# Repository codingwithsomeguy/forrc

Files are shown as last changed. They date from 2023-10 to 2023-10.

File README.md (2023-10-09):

# FORRC - Free and Open RC Robot Car

Welcome to the FORRC repository! FORRC is a basic remote controlled car
that's designed to be a low cost 3d printable car to learn about building
small cars from scratch. The designs are available in FreeCAD and as
exported STL files, and the Bill Of Materials (BOM) is included based
on readily available off the shelf parts.

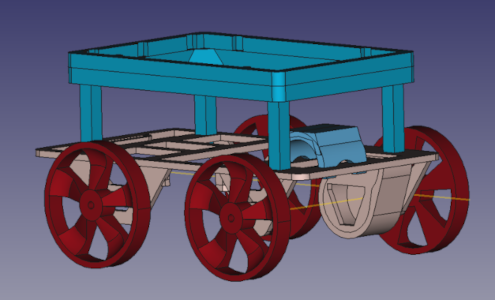
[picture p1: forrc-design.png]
FORRC Design


Note that the FreeCAD file uses the [freecad.gears](https://github.com/looooo/freecad.gears) / FCGear external workbench, available in the Addon Manager.

## Kits
Kits are also available from the Fairfield County Makers' Guild (FCMG)
close to cost, with a small markup for packing/collating and a small
donation. Any profits derived from purchasing a kit goes towards
supporting the FCMG, a 501(c)(3) nonprofit located in Norwalk, CT.
Unless you're purchasing a very large quantity of cars, the kit probably
costs less than buying all of the parts individually, but feel free
to source your own parts! At the time this was created, the kit cost a
bit less, but YMMV. Your support is always appreciated.

## Practical Info
The unmodified base car is geared down for relatively low speeed use.
Feel free to modify the design to add a higher speed motor! For
educational purposes and for the low end microcontroller included, the
lower speeds are easier on the hardware, but it's always fun to go zoom as
well.

The STL files can be loaded into a slicer such as cura but may need to be
flipped over to lie flat on the print bed. Total print time for all the
parts is around 10-20 hours depending on your printer's speed, or the
designs can be sent off to a contract print company for a nominal fee. The
full car (without a body, you'd need to design your own if you want)
takes about 30g of material (test prints were done with PLA).

## Class
If you'd like to build your car and learn about the drive mechanics in person, feel free to sign up for a class at [Fairfield County Makers' Space](https://fcmakers.com) or like minded nearby makerspaces. The course outline will be posted in due time.

## License
These designs, files, and hardware are licensed under the CERN-OHL-S v2 Open Hardware Licence - Strongly Reciprocal. See [License](LICENSE.txt) for the full license text or [CERN's Open Hardware Licence site](https://ohwr.org/cern_ohl_s_v2.txt).

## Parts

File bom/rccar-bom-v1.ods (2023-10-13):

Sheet: BOM
Quantity | Item | Description | Link | Gross Price | Gross Units | Unit Price | Quantity Needed Price
1 | small breadboard | DEYUE breadboard Set Prototype Board - 6 PCS 400 Pin Solderless Board Kit for Raspberry pi and Arduino Project | https://www.amazon.com/dp/B07LFD4LT6 | $7.99 | 6 | $1.33 | $1.33
4 | #61 rubber band | Alliance Rubber 54615 Advantage Rubber Bands Size #61, 1 lb Box Contains Approx. 535 Bands (2inch x 1/4inch, Blue) | https://www.amazon.com/dp/B008X09UNC | $7.58 | 535 | $0.01 | $0.06
1 | MT3608 boost DCDC | 8Pcs DC-DC Adjustable Boost Module 2A DC Voltage Regulator Boost Plate Step Up Converter Module with USB 2V-24V to 5V 9V 12V 28V | https://www.amazon.com/dp/B09ZKKFHXW | $7.99 | 8 | $1.00 | $1.00
1 | battery holder w/leads | QTEATAK 4 x 1.5V AA Batteries Battery Holder Wire Leads | https://www.amazon.com/dp/B085VS14TY | $6.99 | 4 | $1.75 | $1.75
20 | jumpers | AUSTOR 560 Pieces Jumper Wire Kit 14 Lengths Assorted Preformed Breadboard Jumper Wire with Free Box | https://www.amazon.com/dp/B07CJYSL2T | $11.99 | 560 | $0.02 | $0.43
10 | F/M jumper cables long | EDGELEC 120pcs 20cm Dupont Wire Male to Female Breadboard Jumper Wires 7.9 inch 1pin-1pin 2.54mm Connector for DIY Arduino Raspberry PI 10 15 20 30 40 50 100cm Optional Multicolored Ribbon Cables | https://www.amazon.com/dp/B07GD1TFBR | $7.98 | 120 | $0.07 | $0.67
10 | F/M jumper cables short | EDGELEC 120pcs 10cm Dupont Wire Male to Female Breadboard Jumper Wires 3.9 inch 1pin-1pin 2.54mm Connector for DIY Arduino Raspberry PI 10 15 20 30 40 50 100cm Optional Multicolored Ribbon Cables | https://www.amazon.com/dp/B07GD1R5MS | $6.98 | 120 | $0.06 | $0.58
1 | M2 / 10mm | HELIFOUNER 560 Pieces M2 x 4mm /6mm /8mm /10mm /12mm /16mm /20mm, Countersunk Head Socket Cap Screws Bolts Washers Nuts Kit, 304 Stainless Steel | https://www.amazon.com/dp/B0B6HZX2ZJ | $11.99 | 140 | $0.09 | $0.09
2 | M2 / 8mm | (same set) |  |  |  | $0.09 | $0.17
2 | M2 Nuts | (same set)
1 | flyback diode 4004 | BOJACK 1N4004 Rectifier Diode 1 A 400 V DO-41 Axial 4004 1 amp 400 Volt Electronic Silicon Diodes(Pack of 125 Pieces) | https://www.amazon.com/dp/B07Q4F4RPZ | $5.99 | 125 | $0.05 | $0.05
4 | resistors for LEDs | EDGELEC 100pcs 220 ohm Resistor 1/2w (0.5Watt) ±1% Tolerance Metal Film Fixed Resistor, Multiple Values of Resistance Optional | https://www.amazon.com/dp/B07QK9ZBVZ | $5.99 | 100 | $0.06 | $0.24
1 | M2 hex wrench | Tsnamay 2mm Hex Key Wrench L Shaped Hexagon Head Repairing Tool 50pcs | https://www.amazon.com/dp/B09R98WLZ2 | $6.99 | 50 | $0.14 | $0.14
4 | LEDs | BOJACK 5 Colors 500 pcs 5mm LED Diode Lights Assored Kit Pack Bright Lighting Bulb Lamps Electronics Components 5 mm Light Emitting Diodes Parts | https://www.amazon.com/dp/B09XDMJ6KY | $11.99 | 500 | $0.02 | $0.10
1 | BJT | MCIGICM (200 Pcs) 2N2222 Transistor, 2N2222A to-92 Transistor NPN 40V 600mA 300MHz 625mW Through Hole | https://www.amazon.com/dp/B06XPWS52G | $6.99 | 200 | $0.03 | $0.03
1 | L293D motor controller | Bridgold 10pcs L293 L293D 16-pin IC Stepper Motor Drivers Controllers | https://www.amazon.com/dp/B07NXTWJV9 | $8.99 | 10 | $0.90 | $0.90
1 | shift register | (Pack of 25 Pieces) MCIGICM 74HC595 74595 SN74HC595N 8-Bit Shift Register DIP-16 IC 74hc595 Shift registers | https://www.amazon.com/dp/B07HFWB9L9 | $6.99 | 25 | $0.28 | $0.28
1 | esp32cam with CH340C usb card | DORHEA 4 Set ESP32 Cam WiFi Bluetooth Development Board with OV2640 Camera Module + Micro USB to Serial Port CH340C 4.75V-5.25V Nodemcu for Raspberry Pi | https://www.amazon.com/dp/B09265G5Z4 | $28.99 | 4 | $7.25 | $7.25
1 | geared dc N20 motor | Acxico 3Pcs Mini Micro N20 Gear Motor DC 3V-6V Slow Speed Full Metal Gearbox DIY Robot Car | https://www.amazon.com/dp/B09DG3GCGK | $9.99 | 3 | $3.33 | $3.33
1 | steering servo | Sg90 9g Micro Servo Motor, Miuzei Mini Servos Motor Kit Metal Gear 180 Degree Servo for Rc Car Airplane Plane Arduino 10 Pack | https://www.amazon.com/dp/B072V529YD | $18.88 | 10 | $1.89 | $1.89
1 | pack of servo horns | (same set)
1 | cut to 2pc 88mm rods for axles | TOP-VIGOR 20pcs 2mm x 300mm Stainless Steel Rods for DIY Crafts, Metal Solid Round Shaft Rods Lathe Bar Stock for DIY Car Helicopter Airplane Model | https://www.amazon.com//dp/B09WDCDCR6 | $9.59 | 20 | $0.48 | $0.48
48 | PLA | OVERTURE PLA Filament 1.75mm PLA 3D Printer Filament, 2kg Cardboard Spool (4.4lbs), Dimensional Accuracy +/- 0.03mm, Fit Most FDM Printer (White 2-Pack) | https://www.amazon.com/dp/B085DX3X8Y | $36.99 | 2000 | $0.02 | $0.89
 | subtotal with USB programmer |  |  | $227.86 |  |  | $21.64
-1 | esp32cam with CH340C usb card | DORHEA 4 Set ESP32 Cam WiFi Bluetooth Development Board with OV2640 Camera Module + Micro USB to Serial Port CH340C 4.75V-5.25V Nodemcu for Raspberry Pi | https://www.amazon.com/dp/B09265G5Z4 | $28.99 | 4 | $7.25 | -$7.25
1 | esp32cam without USB | 4PCS ESP32-CAM Camera Module ESP32 CAM WiFi Bluetooth Development Board ESP32 Wireless OV2640 Camera Module with Jumper Wire | https://www.amazon.com/dp/B08R8F2BWL | $24.99 | 4 | $6.25 | $6.25 | without the programmer (use an esp8266 or similar)
 | subtotal without USB programmer |  |  |  |  |  | $20.64
Not included:
0.05 | C-A glue | Loctite Super Glue Gel Control, Clear Superglue For Plastic, Wood, Metal, Crafts, & Repair, Cyanoacrylate Adhesive Instant Glue, Quick Dry - 0.14 fl oz Bottle, Pack Of 6 | https://www.amazon.com/dp/B0778LB4RX | $17.16 | 6 | $2.86 | $0.14
1 | small 2mm file | KALIM Mini Needle File Set (Carbon Steel 6 Piece-Set) Hardened Alloy Strength Steel - Set Includes Flat, Flat Warding, Square, Triangular, Round, and Half-Round File(6'' Total Length) | https://www.amazon.com/dp/B07KH8BG1F | $5.99 | 6 | $1.00 | $1.00 | only really need the flat one
4 | AA batteries | Amazon Basics 100-Pack AA Alkaline High-Performance Batteries, 1.5 Volt, 10-Year Shelf Life | https://www.amazon.com/dp/B01B8R6PF2 | $25.76 | 100 | $0.26 | $1.03
 | push buttons

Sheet: Material
qty | part | cura time | time (min) | material (grams) | travel (meters)
1 | rcchassis | 3hr15min | 195 | 16 | 5.38
1 | servocap | 16min | 16 | 2 | 0.54
4 | rubberbandwheel | 3hr7min | 187 | 15 | 5.15
1 | motorclip | 24min | 24 | 2 | 0.68
1 | electronicsriser | 2hrs13min | 133 | 13 | 4.43 | Figuring the total time in friendly units:
2 | axleouterspacer | 6min | 6 | 0.4 | 0.13 | total time (fract) | hours | fractional hours | minutes
 |  |  |  |  |  | 9.35 | 9 | 0.35 | 21
 | total | 9hrs21min | 561 | 48 | 16.18

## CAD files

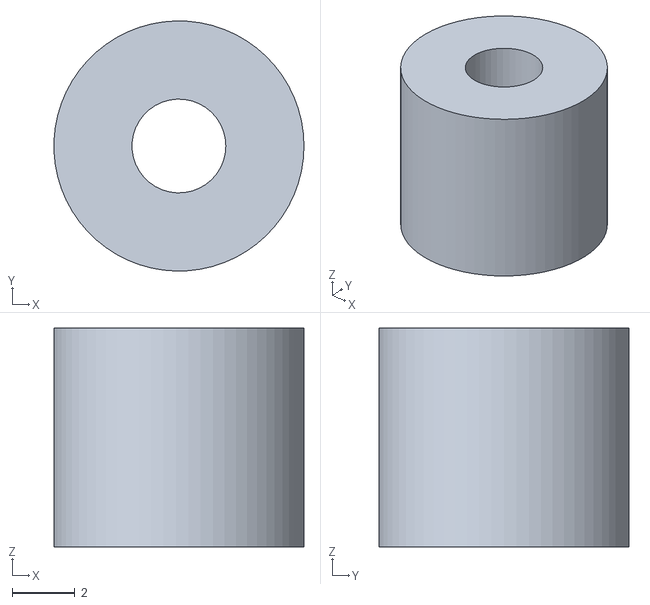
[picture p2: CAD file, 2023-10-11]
exported/axleouterspacer.stl
8.00 x 8.00 x 7.00

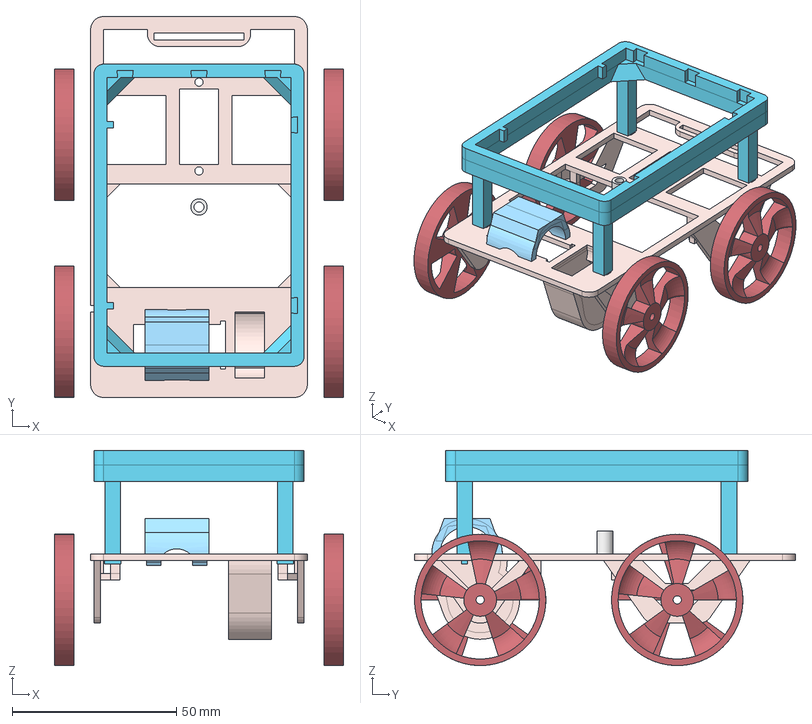
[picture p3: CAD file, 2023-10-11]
rccarchassis.FCStd
88.0 x 116.0 x 65.5 mm
rcchassis
motorclip
rbw-BR
rbw-BL
rbw-FR
rbw-FL
electronicsriser
axleouterspacer

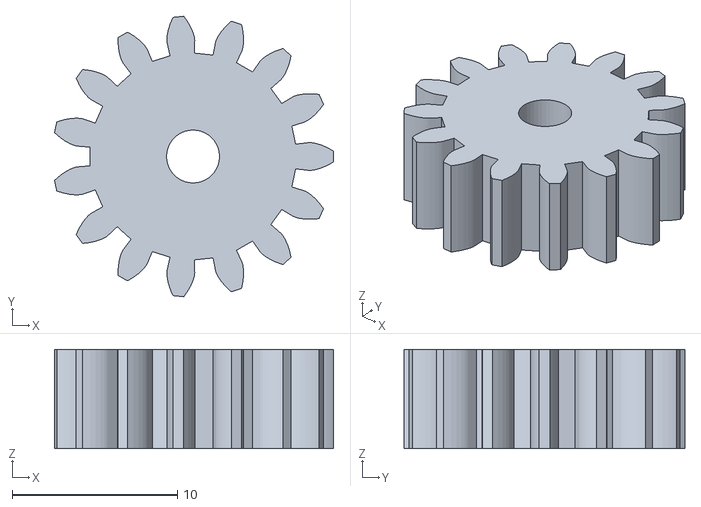
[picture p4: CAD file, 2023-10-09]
exported/drivegear.stl
16.9 x 17.0 x 6.00

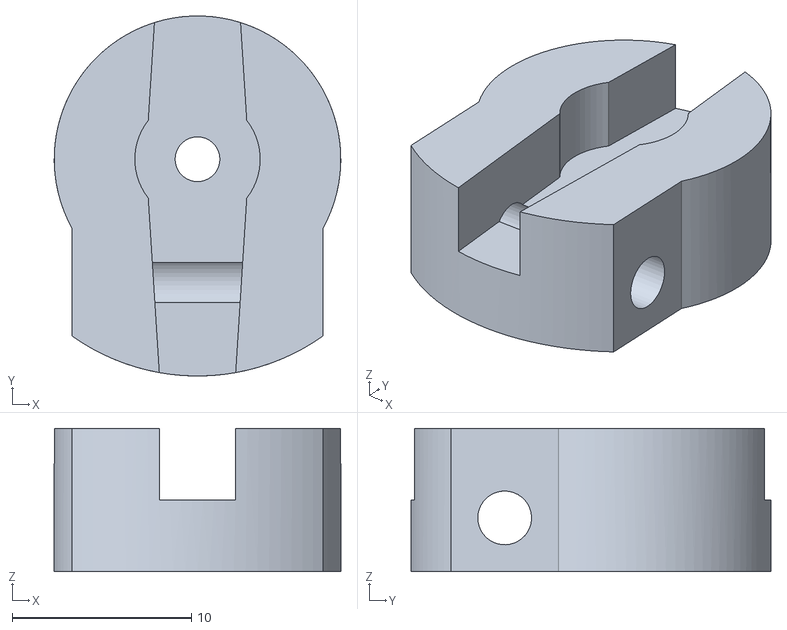
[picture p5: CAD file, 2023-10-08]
exported/simplesteeringservocap.stl
16.0 x 20.1 x 8.00

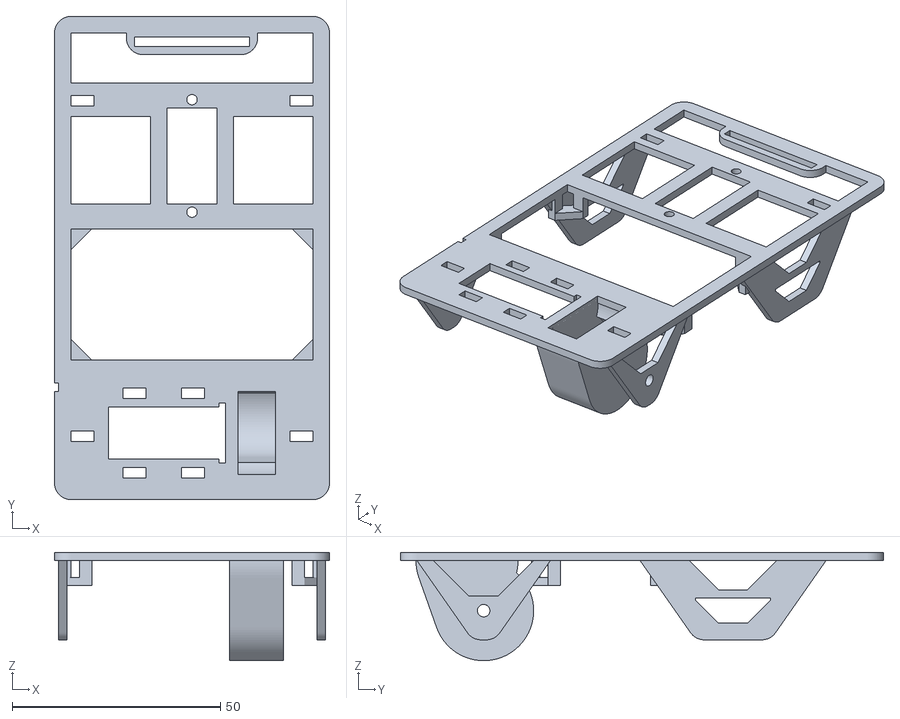
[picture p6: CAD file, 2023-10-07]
exported/rcchassis.stl
66.0 x 116.0 x 26.0

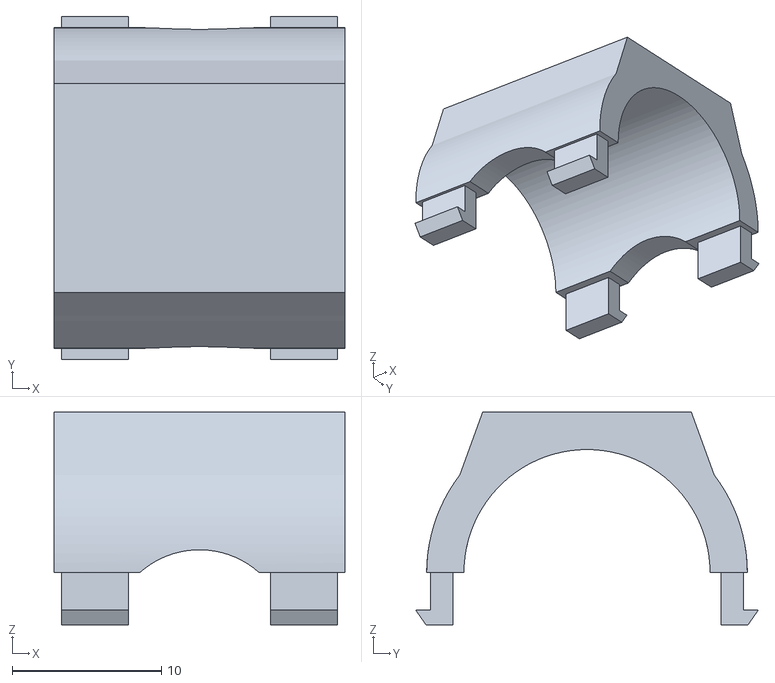
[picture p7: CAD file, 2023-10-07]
exported/motorclip.stl
19.5 x 23.0 x 14.2

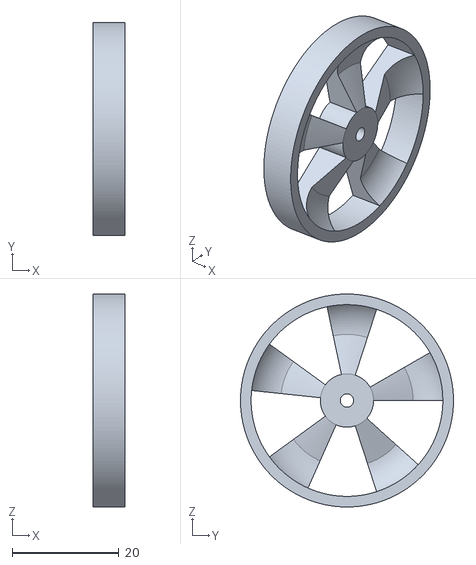
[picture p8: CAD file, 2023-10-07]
exported/rubberbandwheel.stl
6.00 x 40.0 x 40.0

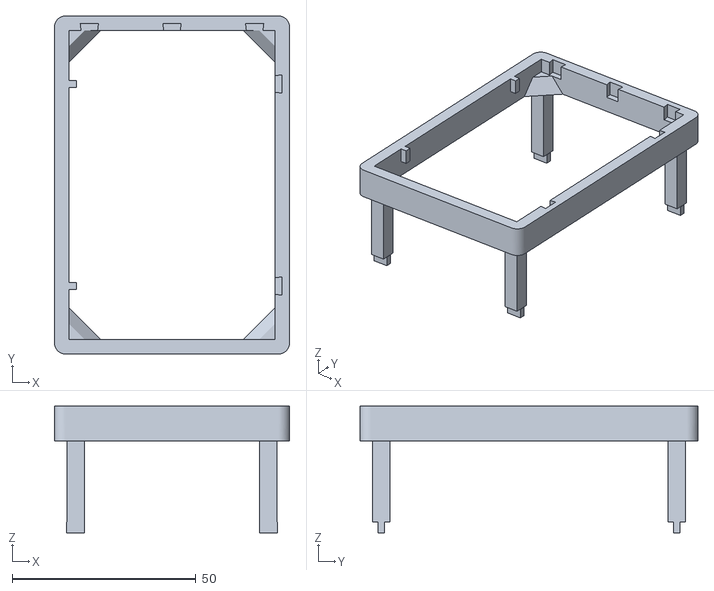
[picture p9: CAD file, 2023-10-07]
exported/electronicsriser.stl
64.0 x 92.0 x 34.5

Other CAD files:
exported/motorgear.stl

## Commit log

2023-10-08 added simple steering servo horn cap
    [rccarchassis.FCStd, simplesteeringservocap.stl]
2023-10-08 github quoting nit
    [rccar-bom-v1.csv, rccar-bom-v1.ods]
2023-10-08 updated material quantities in the bom
    [rccar-bom-v1.csv, rccar-bom-v1.ods]
2023-10-09 added the gears
    [drivegear.stl, motorgear.stl, rccarchassis.FCStd]
2023-10-11 added the drive wheel spacer
    [axleouterspacer.stl, rccar-bom-v1.csv, rccar-bom-v1.ods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]
2023-10-13 added the spacer to the BOM
    [rccar-bom-v1.csv, rccar-bom-v1.ods, rccar-bom-v1.xlsx]
